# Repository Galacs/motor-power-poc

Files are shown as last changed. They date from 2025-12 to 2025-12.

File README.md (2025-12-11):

# Motor Power POC

Motor Power POC board made to test power protection circuits (OCP, UVLO, OVL, RPP...), high current step-down power supply design, rf switch connectors, external FETs H-bridge and power muxes.

## IC List

- ESP32-S3Fx (Main MCU)
- QRE1113 (reflectance sensor)
- LM74502H (Vin RPP)
- TPS56A37 (12v Vout 10A)
- TPS5430 (5v Vout 2.5A)
- LDL212 (3v3 LDO)
- CJ431 (3v shunt reference)
- TPS2121 (5v power mux)
- DRV8701 (H-bridge gate driver)
- SIS412DN-T1-GE3 (10A MOSFET)

## Top preview



## Preview 3d render



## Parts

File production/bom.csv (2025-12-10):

Designator | Footprint | Quantity | Value | LCSC Part #
AE1 | Johanson_2450AT18x100 | 1 | Antenna | C127629
C1, C5 | 0402 | 2 | 12p | C1547
C10, C7 | 0402 | 2 | 1p2 | C76899
C12, C19, C36, C37, C39, C40, C42, C9 | 0402 | 8 | 1u | C52923
C13, C15, C16, C17, C2, C22, C29, C3, C32, C4, C41, C44 | 0402 | 12 | 0u1 | C307331
C20, C21, C30, C31 | 1206 | 4 | 47u | C96123
C23 | 0402 | 1 | 220n | C16772
C24, C25, C26, C28 | 0805 | 4 | 10u | C440198
C27 | 0402 | 1 | 10n | C15195
C33 | 0402 | 1 | 47p | C1567
C34, C35 | 0805 | 2 | 22u | C45783
C38 | 0402 | 1 | 4u7 | C23733
C43 | CP_Elec_6.3x7.7 | 1 | 220u | C46550411
C8 | 0402 | 1 | 10u | C15525
D1, D2, D3, D4, D5 | Diode_DFN1006 | 5 | H5VU10U | C22395519
D6 | D_SMB | 1 | D_TVS | C2925441
D7 | D_SMA | 1 | SS34 | C8678
D8 | 0603 | 1 | RED | C2286
D9 | D_SOD-123 | 1 | BZT52B3V3 | C19077392
J2 | USB_C_Receptacle_HRO_TYPE-C-31-M-12 | 1 | USB_C_Receptacle_USB2.0_14P | C393939
L1 | 0402 | 1 | 24n | C167472
L2 | 0402 | 1 | 6n8 | C77110
L4, L5 | 0402 | 2 | 2n7 | C77108
L6 | L_Sunlord_SWRB1207S | 1 | 18u | C73501
L7 | L_Sunlord_MWSA0804S | 1 | 5u6 | C17700168
Q1, Q10, Q2, Q3, Q4, Q5, Q6, Q7, Q8, Q9 | Vishay_PowerPAK_1212-8_Single | 10 | Q_NMOS | C111309
R1, R2, R3 | 0603 | 3 | 6k8 | C23212
R10, R11 | 0402 | 2 | 22 | C25092
R12, R17, R21, R26, R27, R29, R30, R32, R34, R35, R40, R43, R46, R48, R7, R9 | 0402 | 16 | 10k | C25744
R13, R14, R18, R25 | 0402 | 4 | 5k1 | C25905
R15, R19, R28 | 0402 | 3 | 100k | C25741
R16 | 0603 | 1 | 3k6 | C22980
R20 | 0603 | 1 | 110k | C25805
R22 | 0402 | 1 | 3k3 | C25890
R23, R24 | 0402 | 2 | 2k2 | C25879
R31 | 0603 | 1 | 6k2 | C4260
R33 | 0402 | 1 | 22k | C25768
R36, R49, R6 | 0603 | 3 | 100 | C22775
R37 | 0805 | 1 | 5.1 | C17724
R38 | 0603 | 1 | 10k | C25804
R39 | 0603 | 1 | 50k | C23184
R4 | 0603 | 1 | 47 | C23182
R41 | 0402 | 1 | 33k | C25779
R42 | 0402 | 1 | 200k | C25764
R44 | 0402 | 1 | 68k | C36871
R45 | 0603 | 1 | 7k5 | C23234
R47 | 2512 | 1 | 20m | C5375467
R5 | 0603 | 1 | 75 | C4275
R50 | 0402 | 1 | 0 | C17168
R8 | 0402 | 1 | 470 | C25117
SW1, SW2 | SW_SPST_TS-1088-xR020 | 2 | SW_Push | C720477
TP1, TP10, TP11, TP2, TP3, TP4, TP5, TP6, TP7, TP8, TP9 | TestPoint_Keystone_5015_Micro_Mini | 11 | TestPoint | C2906768
TP12 | Murata_MM8030-26102610 | 1 | RF_switch_connector | C91632
U1, U2, U3 | OnSemi_CASE100CY | 3 | QRE1113GR | C232862
U10 | SOT-23 | 1 | CJ431 | C3113
U11 | Texas_RGE0024H_VQFN-24-1EP_4x4mm_P0.5mm_EP2.7x2.7mm_ThermalVias | 1 | DRV8701 | C90964
U4 | QFN-56-1EP_7x7mm_P0.4mm_EP4x4mm_ThermalVias | 1 | ESP32-S3FH4R2 | C3013940
U5 | SOT-23-THIN-8 | 1 | LM74502 | C3236215
U6 | TI_SO-PowerPAD-8_ThermalVias | 1 | TPS5430DDA | C9864
U7 | Texas_RPA0010A_VQFN-HR-10_3x3mm_P0.5mm | 1 | TPS56A37 | C22392669
U8 | Texas_VQFN-HR-12_2x2.5mm_P0.5mm | 1 | TPS2121 | C485916
U9 | DFN-6-1EP_2x2mm_P0.5mm_ST | 1 | LDL212PV33R | C2969892
Y1 | Crystal_SMD_2016-4Pin_2.0x1.6mm | 1 | 48M | C7206306

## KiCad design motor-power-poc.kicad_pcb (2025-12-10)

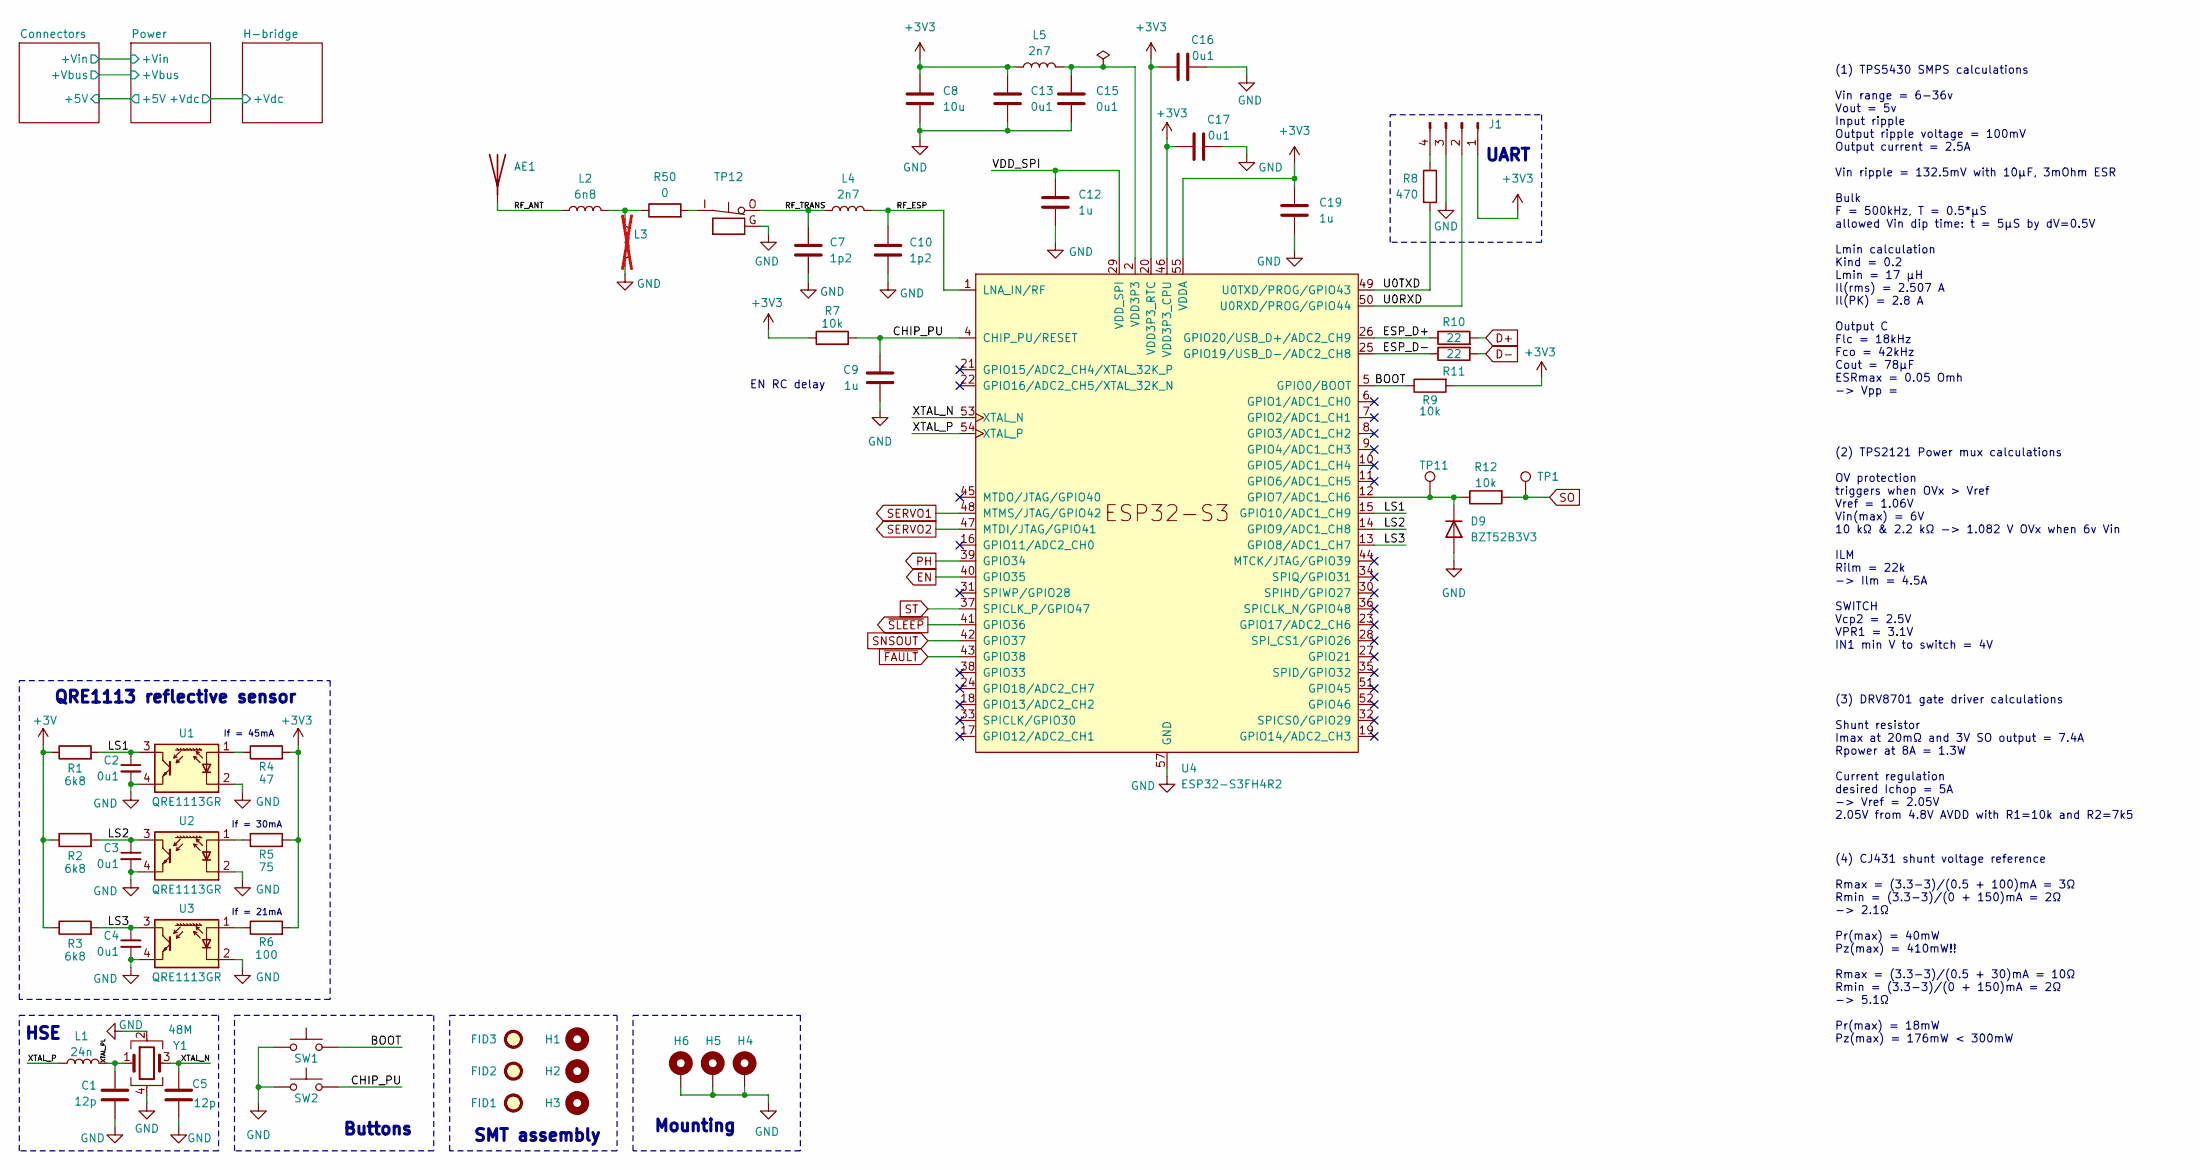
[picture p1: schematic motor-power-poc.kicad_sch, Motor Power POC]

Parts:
AE1: Antenna; Johanson_2450AT18x100; Manufacturer Part Number RFANT3216120A5T; JLCPCB Part # C127629
C1, C5: 12p; C_0402_1005Metric; Manufacturer Part Number 0402CG120J500NT; JLCPCB Part # C1547
C2, C3, C4, C13, C15, C16, C17: 0u1; C_0402_1005Metric; Manufacturer Part Number CL05B104KB54PNC; JLCPCB Part # C307331
C7, C10: 1p2; C_0402_1005Metric; Manufacturer Part Number GJM1555C1H1R2WB01D; JLCPCB Part # C76899
C8: 10u; C_0402_1005Metric; Manufacturer Part Number CL05A106MQ5NUNC; JLCPCB Part # C15525
C9, C12, C19: 1u; C_0402_1005Metric; Manufacturer Part Number CL05A105KA5NQNC; JLCPCB Part # C52923
D9: BZT52B3V3; D_SOD-123; Manufacturer Part Number BZT52B3V3; JLCPCB Part # C19077392
FID1, FID2, FID3: Fiducial; Fiducial_1mm_Mask2mm
H1, H2, H3: MountingHole; ToolingHole_1.152mm
H4, H5, H6: MountingHole_Pad; MountingHole_2.2mm_M2_Pad_Via
J1: Conn_01x04_Pin; PinHeader_1x04_P2.54mm_Vertical
L1: 24n; L_0402_1005Metric; Manufacturer Part Number LQW15AN24NG00D; JLCPCB Part # C167472
L2: 6n8; L_0402_1005Metric; Manufacturer Part Number LQG15HS6N8J02D; JLCPCB Part # C77110
L3: L; L_0402_1005Metric; not fitted
L4, L5: 2n7; L_0402_1005Metric; Manufacturer Part Number LQG15HS2N7S02D; JLCPCB Part # C77108
R1, R2, R3: 6k8; R_0603_1608Metric; Manufacturer Part Number 0603WAF6801T5E; JLCPCB Part # C23212
R4: 47; R_0603_1608Metric; Manufacturer Part Number 0603WAF470JT5E; JLCPCB Part # C23182
R5: 75; R_0603_1608Metric; Manufacturer Part Number 0603WAF750JT5E; JLCPCB Part # C4275
R6: 100; R_0603_1608Metric; Manufacturer Part Number 0603WAF1000T5E; JLCPCB Part # C22775
R7, R9, R12: 10k; R_0402_1005Metric; Manufacturer Part Number 0402WGF1002TCE; JLCPCB Part # C25744
R8: 470; R_0402_1005Metric; Manufacturer Part Number 0402WGF4700TCE; JLCPCB Part # C25117
R10, R11: 22; R_0402_1005Metric; Manufacturer Part Number 0402WGF220JTCE; JLCPCB Part # C25092
R50: 0; R_0402_1005Metric; Manufacturer Part Number 0402WGF0000TCE; JLCPCB Part # C17168
SW1, SW2: SW_Push; SW_SPST_TS-1088-xR020; Manufacturer Part Number TS-1088-AR02016; JLCPCB Part # C720477
TP1, TP11: TestPoint; TestPoint_Keystone_5015_Micro_Mini; Manufacturer Part Number 5015; JLCPCB Part # C2906768
TP12: RF_switch_connector; Murata_MM8030-26102610; Manufacturer Part Number MM8030-2610RK0; JLCPCB Part # C91632
U1, U2, U3: QRE1113GR; OnSemi_CASE100CY; Manufacturer Part Number QRE1113GR; JLCPCB Part # C232862
U4: ESP32-S3FH4R2; QFN-56-1EP_7x7mm_P0.4mm_EP4x4mm_ThermalVias; Manufacturer Part Number ESP32-S3FH4R2; JLCPCB Part # C3013940
Y1: 48M; Crystal_SMD_2016-4Pin_2.0x1.6mm; Manufacturer Part Number R940000096; JLCPCB Part # C7206306

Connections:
+3V: R1.1, R2.1, R3.1; also elsewhere on the board
+3V3: C8.1, C13.1, C16.1, C17.1, C19.1, J1.1, L5.1, R4.2, R5.2, R6.2, R7.1, R9.2, U4.20 (VDD3P3_RTC), U4.46 (VDD3P3_CPU), U4.55 (VDDA), U4.56 (VDDA); also elsewhere on the board
/BOOT: R9.1, SW1.2, U4.5 (GPIO0/BOOT)
/CHIP_PU: C9.1, R7.2, SW2.2, U4.4 (CHIP_PU/RESET)
/ESP_D+: R10.1, U4.26 (GPIO20/USB_D+/ADC2_CH9)
/ESP_D-: R11.1, U4.25 (GPIO19/USB_D-/ADC2_CH8)
/LS1: C2.1, R1.2, U1.3, U4.15 (GPIO10/ADC1_CH9)
/LS2: C3.1, R2.2, U2.3, U4.14 (GPIO9/ADC1_CH8)
/LS3: C4.1, R3.2, U3.3, U4.13 (GPIO8/ADC1_CH7)
/RF_ANT: AE1.1 (A), L2.1
/RF_ESP: C10.1, L4.2, U4.1 (LNA_IN/RF)
/RF_TRANS: C7.1, L4.1, TP12.O
/U0RXD: J1.2, U4.50 (U0RXD/PROG/GPIO44)
/U0TXD: R8.2, U4.49 (U0TXD/PROG/GPIO43)
/VDD_SPI: C12.1, U4.29 (VDD_SPI)
/XTAL_N: C5.1, U4.53 (XTAL_N), Y1.3
/XTAL_P: L1.1, U4.54 (XTAL_P)
/XTAL_PL: C1.2, L1.2, Y1.1
D+: R10.2; also elsewhere on the board
D-: R11.2; also elsewhere on the board
EN: U4.40 (GPIO35); also elsewhere on the board
GND: C1.1, C2.2, C3.2, C4.2, C5.2, C7.2, C8.2, C9.2, C10.2, C12.2, C13.2, C15.2, C16.2, C17.2, C19.2, D9.2 (A), H4.1, H5.1, H6.1, J1.3, L3.2, SW1.1, SW2.1, TP12.G, U1.2 (K), U1.4, U2.2 (K), U2.4, U3.2 (K), U3.4, U4.57 (GND), Y1.2, Y1.4; also elsewhere on the board
unnamed: D9.1 (K), R12.1, TP11.1, U4.12 (GPIO7/ADC1_CH6)
unnamed: J1.4, R8.1
unnamed: L2.2, L3.1, R50.1
unnamed: R50.2, TP12.I
unnamed: R4.1, U1.1 (A)
unnamed: R5.1, U2.1 (A)
unnamed: R6.1, U3.1 (A)
PH: U4.39 (GPIO34); also elsewhere on the board
SERVO1: U4.48 (MTMS/JTAG/GPIO42); also elsewhere on the board
SERVO2: U4.47 (MTDI/JTAG/GPIO41); also elsewhere on the board
SNSOUT: U4.42 (GPIO37); also elsewhere on the board
SO: R12.2, TP1.1; also elsewhere on the board
ST: U4.37 (SPICLK_P/GPIO47); also elsewhere on the board
VDD3P3: C15.1, L5.2, U4.2 (VDD3P3), U4.3 (VDD3P3)
~FAULT: U4.43 (GPIO38); also elsewhere on the board
~SLEEP: U4.41 (GPIO36); also elsewhere on the board

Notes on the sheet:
SMT assembly
Mounting
If = 30mA
Buttons
EN RC delay
QRE1113 reflective sensor
If = 45mA
HSE
UART
If = 21mA
(3) DRV8701 gate driver calculations Shunt resistor Imax at 20mΩ and 3V SO output = 7.4A Rpower at 8A = 1.3W Current regulation desired Ichop = 5A -> Vref = 2.05V 2.05V from 4.8V AVDD with R1=10k and R2=7k5
(1) TPS5430 SMPS calculations Vin range = 6-36v Vout = 5v Input ripple Output ripple voltage = 100mV Output current = 2.5A Vin ripple = 132.5mV with 10µF, 3mOhm ESR Bulk F = 500kHz, T = 0.5*µS allowed Vin dip time: t = 5µS by dV=0.5V Lmin calculation Kind = 0.2 Lmin = 17 µH Il(rms) = 2.507 A Il(PK)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
(4) CJ431 shunt voltage reference Rmax = (3.3-3)/(0.5 + 100)mA = 3Ω Rmin = (3.3-3)/(0 + 150)mA = 2Ω -> 2.1Ω Pr(max) = 40mW Pz(max) = 410mW!! Rmax = (3.3-3)/(0.5 + 30)mA = 10Ω Rmin = (3.3-3)/(0 + 150)mA = 2Ω -> 5.1Ω Pr(max) = 18mW Pz(max) = 176mW < 300mW
(2) TPS2121 Power mux calculations OV protection triggers when OVx > Vref Vref = 1.06V Vin(max) = 6V 10 kΩ & 2.2 kΩ -> 1.082 V OVx when 6v Vin ILM Rilm = 22k -> Ilm = 4.5A SWITCH Vcp2 = 2.5V VPR1 = 3.1V IN1 min V to switch = 4V

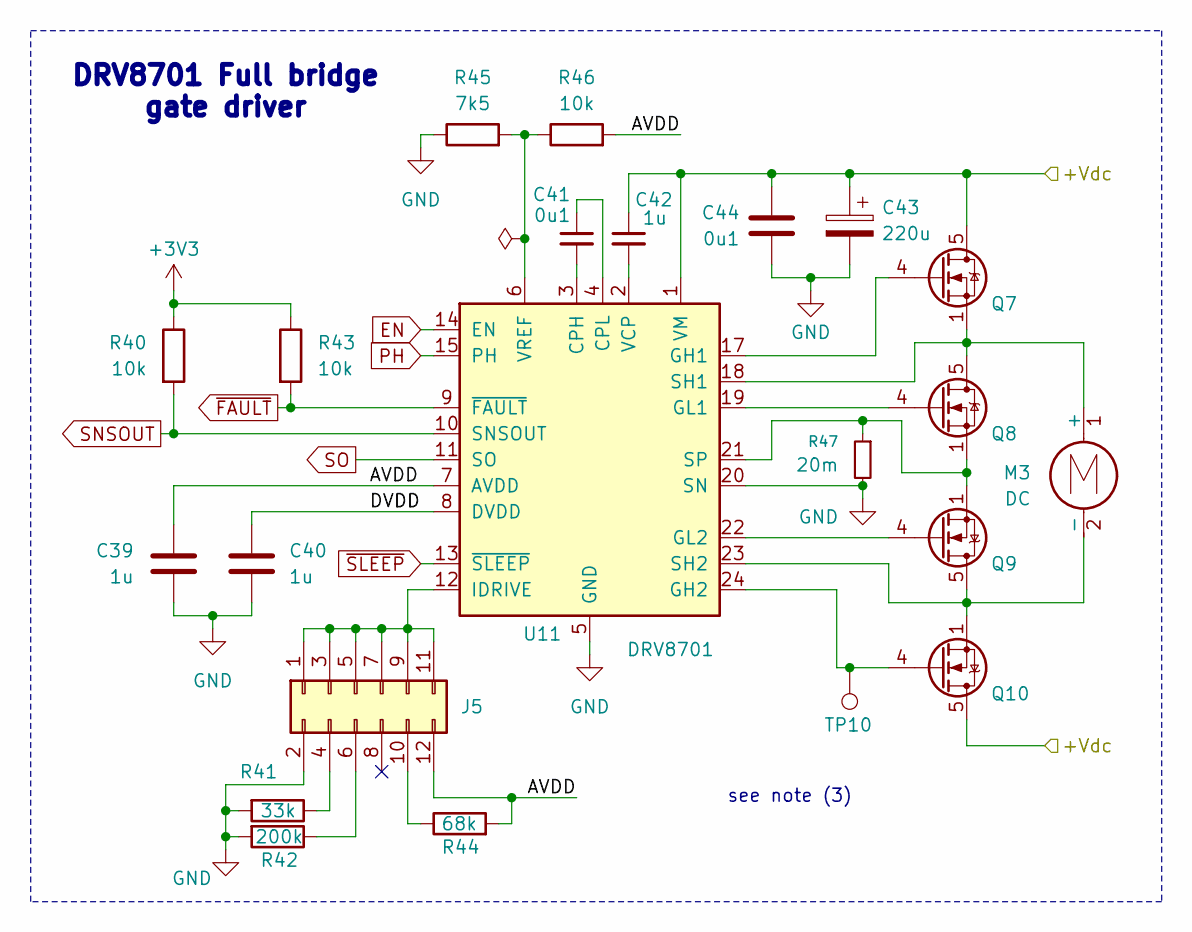
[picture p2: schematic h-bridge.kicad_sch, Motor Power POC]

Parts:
C39, C40, C42: 1u; C_0402_1005Metric; Manufacturer Part Number CL05A105KA5NQNC; JLCPCB Part # C52923
C41, C44: 0u1; C_0402_1005Metric; Manufacturer Part Number CL05B104KB54PNC; JLCPCB Part # C307331
C43: 220u; CP_Elec_6.3x7.7; Manufacturer Part Number JVJ35V220M6x8; JLCPCB Part # C46550411
J5: Conn_02x06_Counter_Clockwise; PinHeader_2x06_P2.54mm_Vertical
M3: DC; TerminalBlock_Phoenix_MKDS-1,5-2-5.08_1x02_P5.08mm_Horizont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
Q7, Q8, Q9, Q10: Q_NMOS; Vishay_PowerPAK_1212-8_Single; Manufacturer Part Number SIS412DN-T1-GE3; JLCPCB Part # C111309
R40, R43, R46: 10k; R_0402_1005Metric; Manufacturer Part Number 0402WGF1002TCE; JLCPCB Part # C25744
R41: 33k; R_0402_1005Metric; Manufacturer Part Number 0402WGF3302TCE; JLCPCB Part # C25779
R42: 200k; R_0402_1005Metric; Manufacturer Part Number 0402WGF2003TCE; JLCPCB Part # C25764
R44: 68k; R_0402_1005Metric; Manufacturer Part Number 0402WGF6802TCE; JLCPCB Part # C36871
R45: 7k5; R_0603_1608Metric; Manufacturer Part Number 0603WAF7501T5E; JLCPCB Part # C23234
R47: 20m; R_2512_6332Metric; Manufacturer Part Number HoYLR2512-3W-20mR-1%; JLCPCB Part # C5375467
TP10: TestPoint; TestPoint_Keystone_5015_Micro_Mini; Manufacturer Part Number 5015; JLCPCB Part # C2906768
U11: DRV8701; Texas_RGE0024H_VQFN-24-1EP_4x4mm_P0.5mm_EP2.7x2.7mm_Thermal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; Manufacturer Part Number DRV8701ERGER; JLCPCB Part # C90964

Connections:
+3V3: R40.1, R43.1; also elsewhere on the board
/H-bridge/+Vdc: C42.1, C43.1, C44.1, Q7.5 (D), Q10.5 (D), U11.1 (VM); also elsewhere on the board
/H-bridge/AVDD: C39.1, J5.12, R44.2, R46.2, U11.7 (AVDD)
/H-bridge/DVDD: C40.1, U11.8 (DVDD)
EN: U11.14 (EN); also elsewhere on the board
GND: C39.2, C40.2, C43.2, C44.2, J5.2, R41.2, R42.2, R45.1, R47.2, U11.5 (GND), U11.16 (GND), U11.20 (SN), U11.25 (GND); also elsewhere on the board
unnamed: J5.1, J5.3, J5.5, J5.7, J5.9, J5.11, U11.12 (IDRIVE)
unnamed: J5.4, R41.1
unnamed: J5.6, R42.1
unnamed: J5.10, R44.1
unnamed: M3.1 (+), Q7.1 (S), Q7.2 (S), Q7.3 (S), Q8.5 (D), U11.18 (SH1)
unnamed: M3.2 (-), Q9.5 (D), Q10.1 (S), Q10.2 (S), Q10.3 (S), U11.23 (SH2)
unnamed: Q7.4 (G), U11.17 (GH1)
unnamed: Q8.4 (G), U11.19 (GL1)
unnamed: Q9.4 (G), U11.22 (GL2)
unnamed: Q10.4 (G), TP10.1, U11.24 (GH2)
unnamed: C41.2, U11.3 (CPH)
unnamed: C41.1, U11.4 (CPL)
unnamed: Q8.1 (S), Q8.2 (S), Q8.3 (S), Q9.1 (S), Q9.2 (S), Q9.3 (S), R47.1, U11.21 (SP)
unnamed: C42.2, U11.2 (VCP)
unnamed: R45.2, R46.1, U11.6 (VREF)
PH: U11.15 (PH); also elsewhere on the board
SNSOUT: R40.2, U11.10 (SNSOUT); also elsewhere on the board
SO: U11.11 (SO); also elsewhere on the board
~FAULT: R43.2, U11.9 (~FAULT); also elsewhere on the board
~SLEEP: U11.13 (~SLEEP); also elsewhere on the board

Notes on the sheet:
see note (3)
DRV8701 Full bridge gate driver

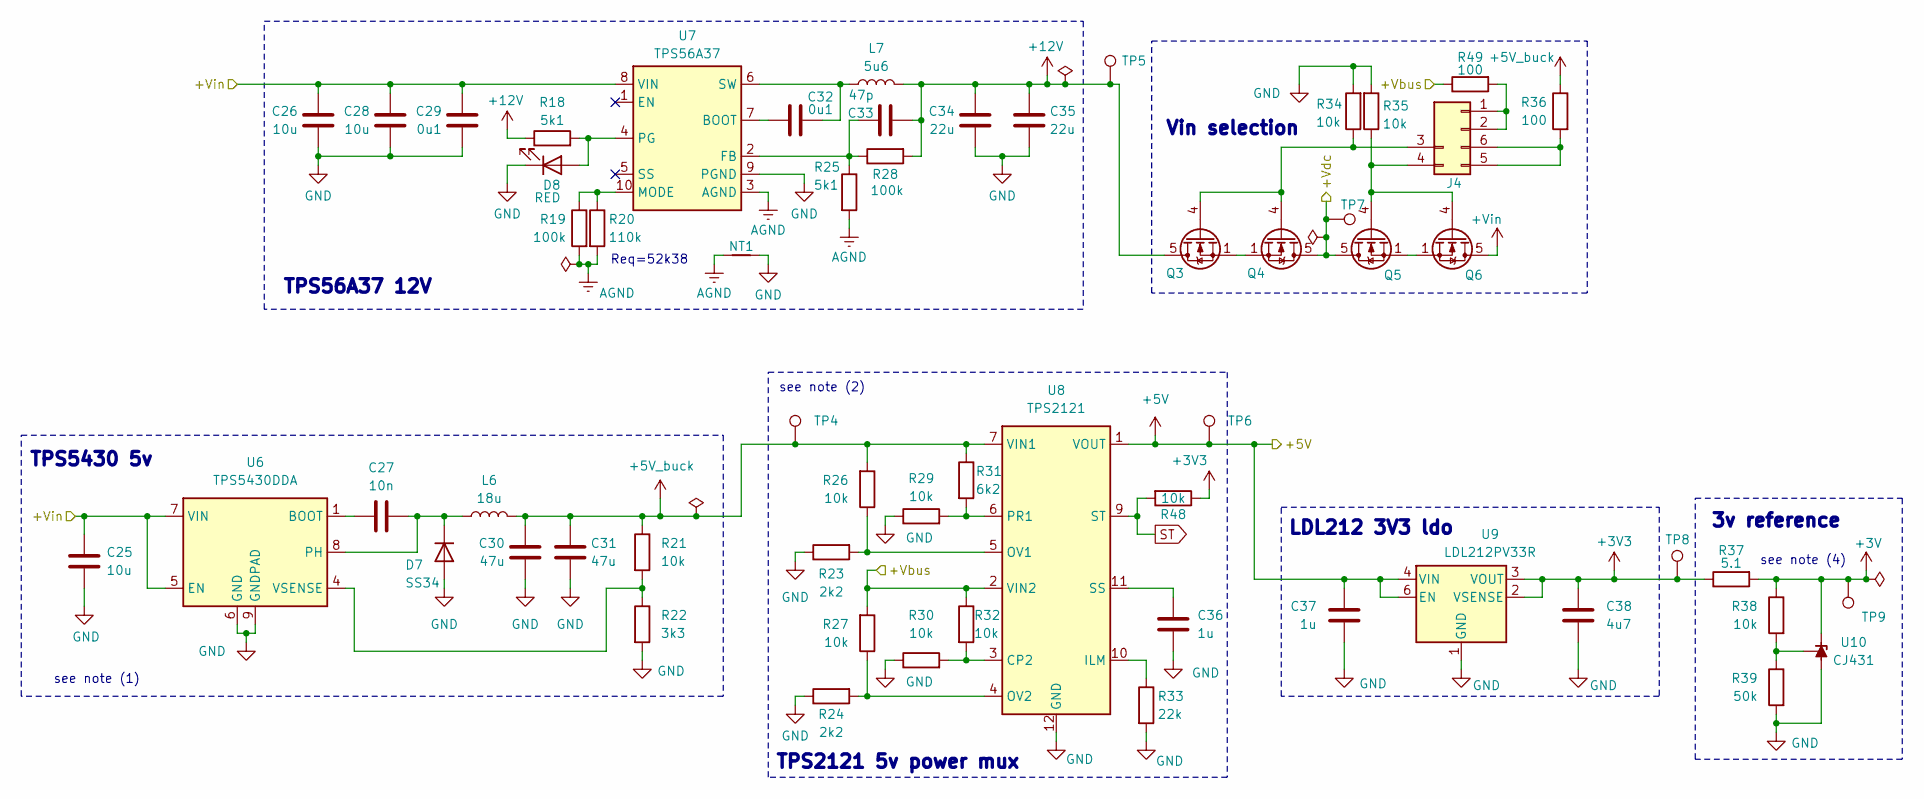
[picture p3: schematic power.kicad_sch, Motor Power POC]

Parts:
C25, C26, C28: 10u; C_0805_2012Metric; Manufacturer Part Number GRM21BR61H106KE43L; JLCPCB Part # C440198
C27: 10n; C_0402_1005Metric; Manufacturer Part Number CL05B103KB5NNNC; JLCPCB Part # C15195
C29, C32: 0u1; C_0402_1005Metric; Manufacturer Part Number CL05B104KB54PNC; JLCPCB Part # C307331
C30, C31: 47u; C_1206_3216Metric; Manufacturer Part Number CL31A476MPHNNNE; JLCPCB Part # C96123
C33: 47p; C_0402_1005Metric; Manufacturer Part Number 0402CG470J500NT; JLCPCB Part # C1567
C34, C35: 22u; C_0805_2012Metric; Manufacturer Part Number CL21A226MAQNNNE; JLCPCB Part # C45783
C36, C37: 1u; C_0402_1005Metric; Manufacturer Part Number CL05A105KA5NQNC; JLCPCB Part # C52923
C38: 4u7; C_0402_1005Metric; Manufacturer Part Number CL05A475MP5NRNC; JLCPCB Part # C23733
D7: SS34; D_SMA; Manufacturer Part Number SS34; JLCPCB Part # C8678
D8: RED; LED_0603_1608Metric; Manufacturer Part Number KT-0603R; JLCPCB Part # C2286
J4: Conn_02x02_Counter_Clockwise; PinHeader_2x03_P2.54mm_Vertical
L6: 18u; L_Sunlord_SWRB1207S; Manufacturer Part Number SWRH1207B-180MT; JLCPCB Part # C73501
L7: 5u6; L_Sunlord_MWSA0804S; Manufacturer Part Number MWSA0804S-5R6MT; JLCPCB Part # C17700168
NT1: NetTie_2; NetTie-2_SMD_Pad0.5mm
Q3, Q4, Q5, Q6: Q_NMOS; Vishay_PowerPAK_1212-8_Single; Manufacturer Part Number SIS412DN-T1-GE3; JLCPCB Part # C111309
R18, R25: 5k1; R_0402_1005Metric; Manufacturer Part Number 0402WGF5101TCE; JLCPCB Part # C25905
R19, R28: 100k; R_0402_1005Metric; Manufacturer Part Number 0402WGF1003TCE; JLCPCB Part # C25741
R20: 110k; R_0603_1608Metric; Manufacturer Part Number 0603WAF1103T5E; JLCPCB Part # C25805
R21, R26, R27, R29, R30, R32, R34, R35, R48: 10k; R_0402_1005Metric; Manufacturer Part Number 0402WGF1002TCE; JLCPCB Part # C25744
R22: 3k3; R_0402_1005Metric; Manufacturer Part Number 0402WGF3301TCE; JLCPCB Part # C25890
R23, R24: 2k2; R_0402_1005Metric; Manufacturer Part Number 0402WGF2201TCE; JLCPCB Part # C25879
R31: 6k2; R_0603_1608Metric; Manufacturer Part Number 0603WAF6201T5E; JLCPCB Part # C4260
R33: 22k; R_0402_1005Metric; Manufacturer Part Number 0402WGF2202TCE; JLCPCB Part # C25768
R36, R49: 100; R_0603_1608Metric; Manufacturer Part Number 0603WAF1000T5E; JLCPCB Part # C22775
R37: 5.1; R_0805_2012Metric; Manufacturer Part Number 0805W8F510KT5E; JLCPCB Part # C17724
R38: 10k; R_0603_1608Metric; Manufacturer Part Number 0603WAF1002T5E; JLCPCB Part # C25804
R39: 50k; R_0603_1608Metric; Manufacturer Part Number 0603WAF4992T5E; JLCPCB Part # C23184
TP4, TP5, TP6, TP7, TP8, TP9: TestPoint; TestPoint_Keystone_5015_Micro_Mini; Manufacturer Part Number 5015; JLCPCB Part # C2906768
U6: TPS5430DDA; TI_SO-PowerPAD-8_ThermalVias; Manufacturer Part Number TPS5430DDAR; JLCPCB Part # C9864
U7: TPS56A37; Texas_RPA0010A_VQFN-HR-10_3x3mm_P0.5mm; Manufacturer Part Number TPS56A37RPAR; JLCPCB Part # C22392669
U8: TPS2121; Texas_VQFN-HR-12_2x2.5mm_P0.5mm; Manufacturer Part Number TPS2121RUXR; JLCPCB Part # C485916
U9: LDL212PV33R; DFN-6-1EP_2x2mm_P0.5mm_ST; Manufacturer Part Number LDL212PV33R; JLCPCB Part # C2969892
U10: CJ431; SOT-23; Manufacturer Part Number CJ431; JLCPCB Part # C3113

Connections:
+3V: R37.2, R38.1, TP9.1, U10.2 (K); also elsewhere on the board
+3V3: C38.1, R37.1, R48.1, TP8.1, U9.2 (VSENSE), U9.3 (VOUT); also elsewhere on the board
+5V: C37.1, TP6.1, U8.1 (VOUT), U8.8 (VOUT), U9.4 (VIN), U9.6 (EN); also elsewhere on the board
+5V_buck: C30.1, C31.1, L6.2, R21.1, R26.2, R31.1, R36.1, TP4.1, U8.7 (VIN1)
+12V: C33.2, C34.1, C35.1, L7.2, Q3.5 (D), R18.1, R28.2, TP5.1
+Vbus: R27.2, R32.1, R49.1, U8.2 (VIN2); also elsewhere on the board
+Vin: C25.1, C26.1, C28.1, C29.1, Q6.5 (D), U6.5 (EN), U6.7 (VIN), U7.8 (VIN); also elsewhere on the board
/H-bridge/+Vdc: Q4.5 (D), Q5.5 (D), TP7.1; also elsewhere on the board
AGND: NT1.1, R19.2, R20.2, R25.2, U7.3 (AGND)
GND: C25.2, C26.2, C28.2, C29.2, C30.2, C31.2, C34.2, C35.2, C36.2, C37.2, C38.2, D7.2 (A), D8.1 (K), NT1.2, R22.2, R23.1, R24.1, R29.1, R30.1, R33.2, R34.2, R35.2, R39.2, U6.6 (GND), U6.9 (GNDPAD), U7.9 (PGND), U8.12 (GND), U9.1 (GND), U10.3 (A); also elsewhere on the board
unnamed: C27.2, D7.1 (K), L6.1, U6.8 (PH)
unnamed: D8.2 (A), R18.2, U7.4 (PG)
unnamed: J4.1, J4.2, R49.2
unnamed: J4.3, Q3.4 (G), Q4.4 (G), R34.1
unnamed: J4.4, Q5.4 (G), Q6.4 (G), R35.1
unnamed: J4.5, J4.6, R36.2
unnamed: Q3.1 (S), Q3.2 (S), Q3.3 (S), Q4.1 (S), Q4.2 (S), Q4.3 (S)
unnamed: Q5.1 (S), Q5.2 (S), Q5.3 (S), Q6.1 (S), Q6.2 (S), Q6.3 (S)
unnamed: C27.1, U6.1 (BOOT)
unnamed: R21.2, R22.1, U6.4 (VSENSE)
unnamed: C32.1, U7.7 (BOOT)
unnamed: C33.1, R25.1, R28.1, U7.2 (FB)
unnamed: R19.1, R20.1, U7.10 (MODE)
unnamed: C32.2, L7.1, U7.6 (SW)
unnamed: R30.2, R32.2, U8.3 (CP2)
unnamed: R33.1, U8.10 (ILM)
unnamed: R23.2, R26.1, U8.5 (OV1)
unnamed: R24.2, R27.1, U8.4 (OV2)
unnamed: R29.2, R31.2, U8.6 (PR1)
unnamed: C36.1, U8.11 (SS)
unnamed: R38.2, R39.1, U10.1 (REF)
ST: R48.2, U8.9 (ST); also elsewhere on the board

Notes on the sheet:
Vin selection
3v reference
TPS2121 5v power mux
LDL212 3V3 ldo
see note (1)
see note (2)
Req=52k38
TPS5430 5v
TPS56A37 12V
see note (4)

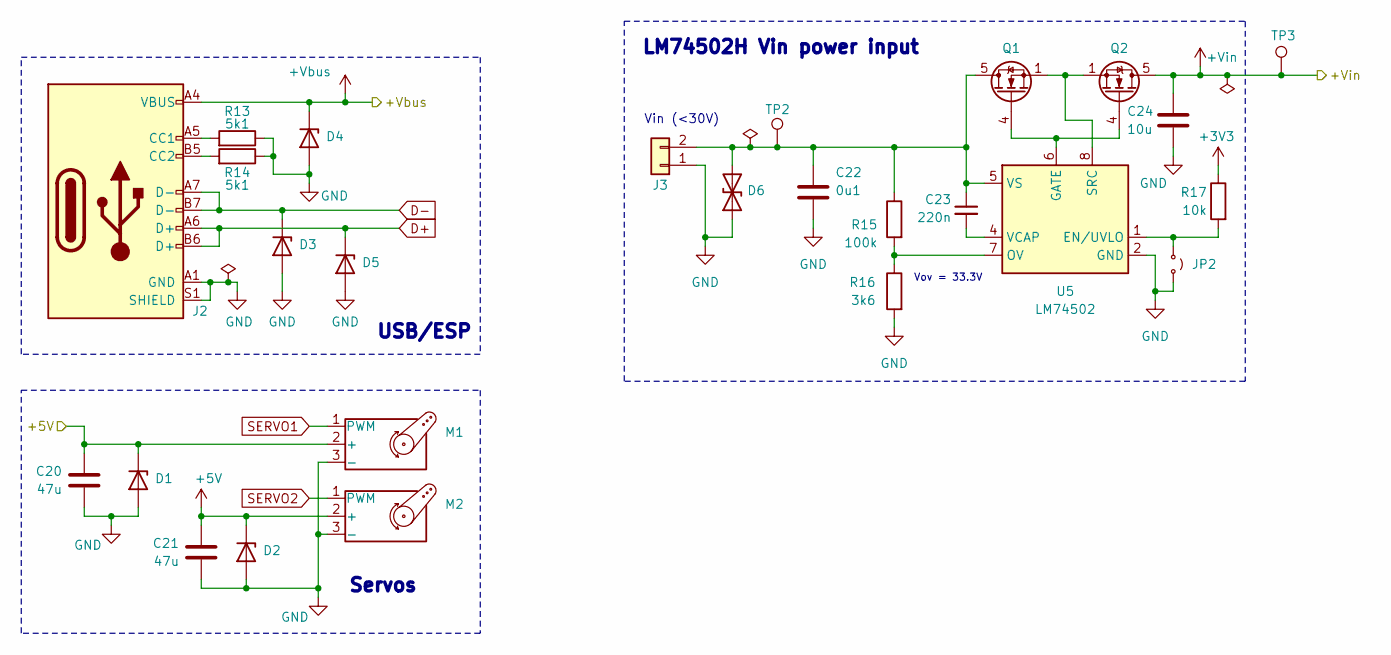
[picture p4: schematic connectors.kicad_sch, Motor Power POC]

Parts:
C20, C21: 47u; C_1206_3216Metric; Manufacturer Part Number CL31A476MPHNNNE; JLCPCB Part # C96123
C22: 0u1; C_0402_1005Metric; Manufacturer Part Number CL05B104KB54PNC; JLCPCB Part # C307331
C23: 220n; C_0402_1005Metric; Manufacturer Part Number CL05B224KO5NNNC; JLCPCB Part # C16772
C24: 10u; C_0805_2012Metric; Manufacturer Part Number GRM21BR61H106KE43L; JLCPCB Part # C440198
D1, D2, D3, D4, D5: H5VU10U; Diode_DFN1006; Manufacturer Part Number H5VU10U; JLCPCB Part # C22395519
D6: D_TVS; D_SMB; Manufacturer Part Number SMBJ30CA; JLCPCB Part # C2925441
J2: USB_C_Receptacle_USB2.0_14P; USB_C_Receptacle_HRO_TYPE-C-31-M-12; Manufacturer Part Number TYPE-C16PIN; JLCPCB Part # C393939
J3: Conn_01x02; TerminalBlock_Phoenix_MKDS-1,5-2-5.08_1x02_P5.08mm_Horizont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
JP2: Jumper_2_Small_Open; PinHeader_1x02_P2.54mm_Vertical
M1, M2: Motor_Servo; PinHeader_1x03_P2.54mm_Vertical
Q1, Q2: Q_NMOS; Vishay_PowerPAK_1212-8_Single; Manufacturer Part Number SIS412DN-T1-GE3; JLCPCB Part # C111309
R13, R14: 5k1; R_0402_1005Metric; Manufacturer Part Number 0402WGF5101TCE; JLCPCB Part # C25905
R15: 100k; R_0402_1005Metric; Manufacturer Part Number 0402WGF1003TCE; JLCPCB Part # C25741
R16: 3k6; R_0603_1608Metric; Manufacturer Part Number 0603WAF3601T5E; JLCPCB Part # C22980
R17: 10k; R_0402_1005Metric; Manufacturer Part Number 0402WGF1002TCE; JLCPCB Part # C25744
TP2, TP3: TestPoint; TestPoint_Keystone_5015_Micro_Mini; Manufacturer Part Number 5015; JLCPCB Part # C2906768
U5: LM74502; SOT-23-THIN-8; Manufacturer Part Number LM74502DDFR; JLCPCB Part # C3236215

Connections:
+3V3: R17.1; also elsewhere on the board
+5V: C20.1, C21.1, D1.1 (K), D2.1 (K), M1.2 (+), M2.2 (+); also elsewhere on the board
+Vbus: D4.1 (K), J2.A4 (VBUS), J2.A9 (VBUS), J2.B4 (VBUS), J2.B9 (VBUS); also elsewhere on the board
+Vin: C24.1, Q2.5 (D), TP3.1; also elsewhere on the board
D+: D5.1 (K), J2.A6 (D+), J2.B6 (D+); also elsewhere on the board
D-: D3.1 (K), J2.A7 (D-), J2.B7 (D-); also elsewhere on the board
GND: C20.2, C21.2, C22.2, C24.2, D1.2 (A), D2.2 (A), D3.2 (A), D4.2 (A), D5.2 (A), D6.1 (A1), J2.A1 (GND), J2.A12 (GND), J2.B1 (GND), J2.B12 (GND), J2.S1 (SHIELD), J3.1, JP2.2 (B), M1.3 (-), M2.3 (-), R13.1, R14.1, R16.2, U5.2 (GND); also elsewhere on the board
unnamed: C22.1, C23.1, D6.2 (A2), J3.2, Q1.5 (D), R15.1, TP2.1, U5.5 (VS)
unnamed: J2.A5 (CC1), R13.2
unnamed: J2.B5 (CC2), R14.2
unnamed: JP2.1 (A), R17.2, U5.1 (EN/UVLO)
unnamed: Q1.4 (G), Q2.4 (G), U5.6 (GATE)
unnamed: R15.2, R16.1, U5.7 (OV)
unnamed: Q1.1 (S), Q1.2 (S), Q1.3 (S), Q2.1 (S), Q2.2 (S), Q2.3 (S), U5.8 (SRC)
unnamed: C23.2, U5.4 (VCAP)
SERVO1: M1.1 (PWM); also elsewhere on the board
SERVO2: M2.1 (PWM); also elsewhere on the board

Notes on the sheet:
Vin (<30V)
Vov = 33.3V
LM74502H Vin power input
USB/ESP
Servos

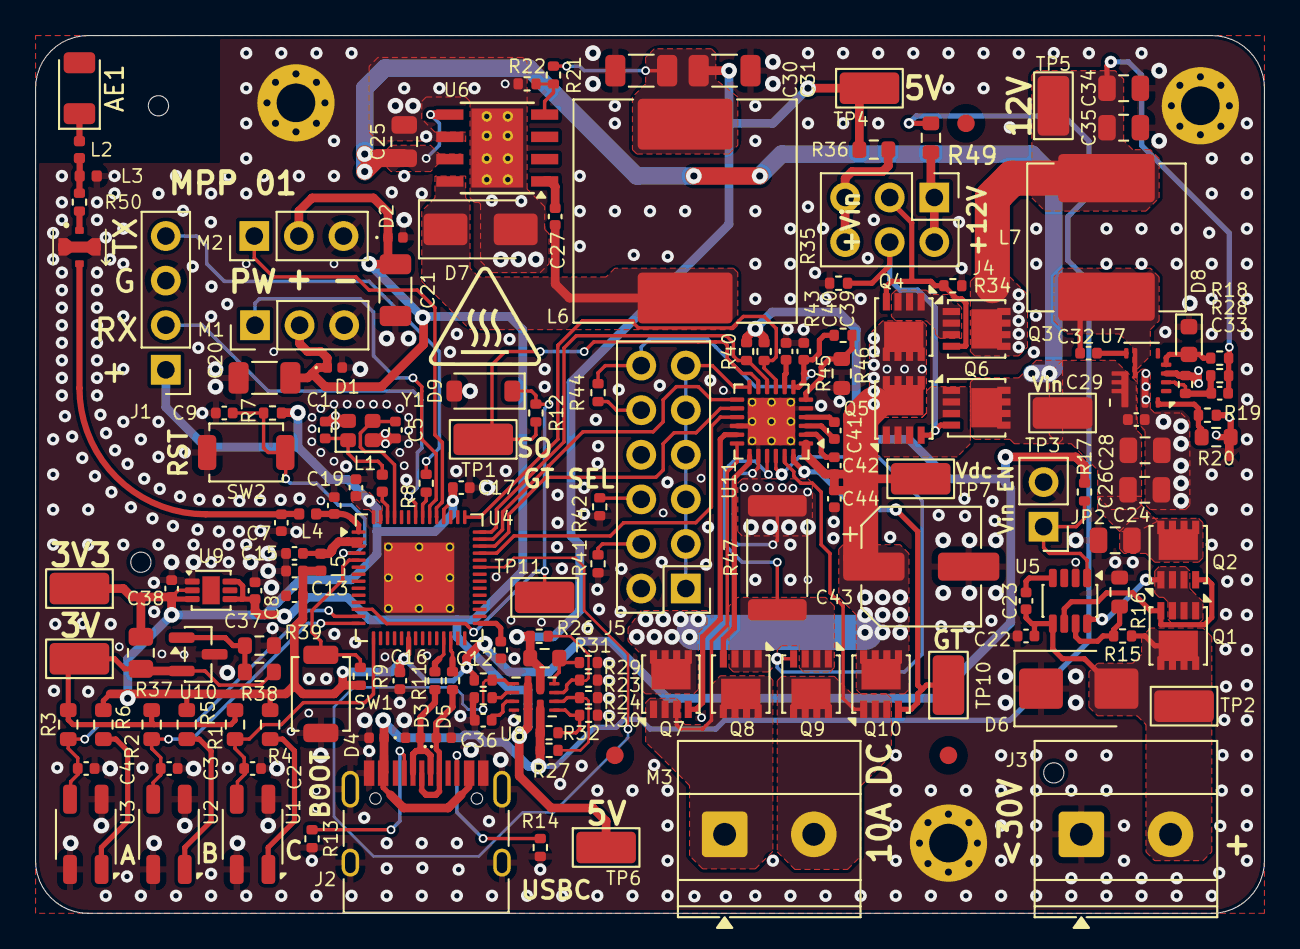
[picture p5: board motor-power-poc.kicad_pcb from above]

Board: 4 copper layers, 70.0 x 50.0 mm, 162 parts (0 on the bottom side), 91 nets.

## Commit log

2025-11-17 schem: import ESP32-S3 and USBC from adbq-usb-temp
    [motor-power-poc.kicad_sch]
2025-11-18 schem: add TPS5430 5v SMPS with calculations note
    [motor-power-poc.kicad_sch]
2025-11-20 schem: add TPS2121 5v power mux
    [motor-power-poc.kicad_sch]
2025-11-21 schem: add TPS2121 5v power mux components values
    [motor-power-poc.kicad_sch]
2025-11-21 schem: update VBUS TVS diode
    [motor-power-poc.kicad_sch]
2025-11-21 schem: add LDL212 3V3 ldo
    [motor-power-poc.kicad_sch]
2025-11-27 schem: moved connectors to separate sheet
    [connectors.kicad_sch, motor-power-poc.kicad_sch]
2025-11-27 schem: moved ldo, smps and power mux to power sheet
    [motor-power-poc.kicad_sch, power.kicad_sch]
2025-11-27 symbol: update footprints library name
    [connectors.kicad_sch]
2025-11-27 schem: add LM74502H Vin power input
    [connectors.kicad_sch]
2025-11-27 schem: add servos connectors
    [connectors.kicad_sch]
2025-11-28 schematic: DRV8701 Full bridge gate driver
    [connectors.kicad_sch, h-bridge.kicad_sch, motor-power-poc.kicad_sch]
2025-11-29 schem: add DRV8701 component values
    [h-bridge.kicad_sch, motor-power-poc.kicad_sch]
2025-11-29 schem: add LM74502H enable jumper
    [connectors.kicad_sch]
2025-11-29 schem: add TPS56A37 components values
    [power.kicad_sch]
2025-11-29 schem: add Vin driver input selection circuit
    [connectors.kicad_sch, h-bridge.kicad_sch, power.kicad_sch]
2025-11-29 schem: move selection circuit
    [power.kicad_sch]
2025-11-29 schem: changed selection circuit to back to back fets
    [power.kicad_sch]
2025-11-29 schem: add QRE1113 reflective sensor
    [motor-power-poc.kicad_sch]
2025-11-30 schem: add 3v reference
    [motor-power-poc.kicad_sch, power.kicad_sch]
2025-11-30 schem: add pins to hierachical sheets
    [connectors.kicad_sch, h-bridge.kicad_sch, motor-power-poc.kicad_sch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]
2025-11-30 schem: add +Vbus to hierachical
    [connectors.kicad_sch, motor-power-poc.kicad_sch, power.kicad_sch]
2025-11-30 schem: add +5V to hierachical
    [connectors.kicad_sch, motor-power-poc.kicad_sch, power.kicad_sch]
2025-11-30 schem: connect dc driver to mcu and add no connects
    [connectors.kicad_sch, motor-power-poc.kicad_sch]
2025-11-30 schem: add test points
    [connectors.kicad_sch, motor-power-poc.kicad_sch, power.kicad_sch]
2025-11-30 schem: fix peripherals using flash ESP32 pins
    [motor-power-poc.kicad_sch]
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2025-11-30 schem: run and fix ERC
    [connectors.kicad_sch, h-bridge.kicad_sch, motor-power-poc.kicad_sch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]
2025-11-30 schem: add net classes
    [motor-power-poc.kicad_sch]
2025-11-30 schem: import UART connector from esp32c6-sensor-devboard
    [motor-power-poc.kicad_sch]
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2025-12-01 schem: add connectors footprint
    [connectors.kicad_sch, h-bridge.kicad_sch]
2025-12-01 schem: add ordering info to BOM
    [connectors.kicad_sch, h-bridge.kicad_sch, motor-power-poc.kicad_sch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]
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2025-12-02 pcb: import 4 layer stackup
    [motor-power-poc.kicad_pcb]
2025-12-02 schem: update MOSFETs symbol
    [connectors.kicad_sch, h-bridge.kicad_sch, power.kicad_sch]
2025-12-02 schem: fix DRV8701 gnd pad pin number
    [h-bridge.kicad_sch]
2025-12-02 pcb: import from schematic
    [motor-power-poc.kicad_pcb]
2025-12-02 pcb: add missing 3d models
    [motor-power-poc.kicad_pcb]
2025-12-02 pcb: initial rough placement
    [motor-power-poc.kicad_pcb]
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2025-12-02 schem: update MOSFETs footprints to correct N-channel
    [connectors.kicad_sch, h-bridge.kicad_sch, power.kicad_sch]
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2025-12-02 pcb: add LM74502 RPP layout
    [motor-power-poc.kicad_pcb]
2025-12-03 pcb: add TPS56A37 layout
    [motor-power-poc.kicad_pcb]
2025-12-03 schem: add 0u1 decoupling cap to DRV8701
    [h-bridge.kicad_sch]
2025-12-03 pcb: add DRV8701 layout
    [motor-power-poc.kicad_pcb]
2025-12-03 pcb: add 3v3 and 3v layout
    [motor-power-poc.kicad_pcb]
2025-12-03 pcb: add QR113 layout
    [motor-power-poc.kicad_pcb]
2025-12-03 schem: connect TPS2121 ST pin to MCU
    [motor-power-poc.kicad_sch, power.kicad_sch]
2025-12-03 pcb: add TPS2121 layout
    [motor-power-poc.kicad_pcb]
2025-12-03 pcb: add TPS5430 layout
    [motor-power-poc.kicad_pcb, motor-power-poc.kicad_sch]
2025-12-03 schem: remove extra decoupling caps
    [motor-power-poc.kicad_sch]
2025-12-03 pcb: add mcu decoupling caps layout
    [motor-power-poc.kicad_pcb]
2025-12-03 pcb: add board outline
    [motor-power-poc.kicad_pcb]
2025-12-03 schem: add fiduals, tooling and mounting holes
    [motor-power-poc.kicad_sch]
2025-12-03 pcb: add fiducials, tooling holes and mounting holes
    [motor-power-poc.kicad_pcb]
2025-12-03 schem: add DRV8701 gate test point
    [h-bridge.kicad_sch]
2025-12-03 pcb: add inner gnd planes
    [motor-power-poc.kicad_pcb]
2025-12-03 schem: use espressif QFN-56 footprint for ESP32S3 MCU
    [motor-power-poc.kicad_sch]
2025-12-03 pcb: add gns vias
    [motor-power-poc.kicad_pcb]
2025-12-03 pcb: set grid and drill origins
    [motor-power-poc.kicad_pcb]
2025-12-03 schem: ESP32 pin reorganisation
    [motor-power-poc.kicad_pcb, motor-power-poc.kicad_sch]
2025-12-03 pcb: add rf routing
    [motor-power-poc.kicad_pcb]
2025-12-03 pcb: add crystal routing
    [motor-power-poc.kicad_pcb]
2025-12-03 pcb: add USB routing
    [motor-power-poc.kicad_pcb]
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2025-12-05 pcb: run and fix DRC
    [motor-power-poc.kicad_pcb, power.kicad_sch]
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2025-12-06 schem: fix BOM
    [bom.csv, connectors.kicad_sch, motor-power-poc.kicad_pcb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]
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2025-12-10 pcb: move hot warning to avoid exposing Vin
    [motor-power-poc.kicad_pcb]
2025-12-10 schem: remove circular dependency for vin sel gate
    [power.kicad_sch]
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2025-12-10 schem: change antenna to available and add rf switch connector
    [motor-power-poc.kicad_sch, power.kicad_sch]
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
